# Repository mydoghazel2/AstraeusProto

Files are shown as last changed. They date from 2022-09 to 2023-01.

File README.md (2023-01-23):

# Astraeus

This is the github repo of the West Virginia University SRAD avionics project named Astraeus.

Astreaus is a student led project to develop cheap, open-source, and modular avionics. The goal is to create electronics for our competition rocket and for student use on personal rockets. 

Astraeus is the greek god of the wind and dusk to match not only the idea of our avionics being on a rocket but also our competition rocket being named "Dark and Dusty" after the song Country Roads 

# Final Design 
## Top Side
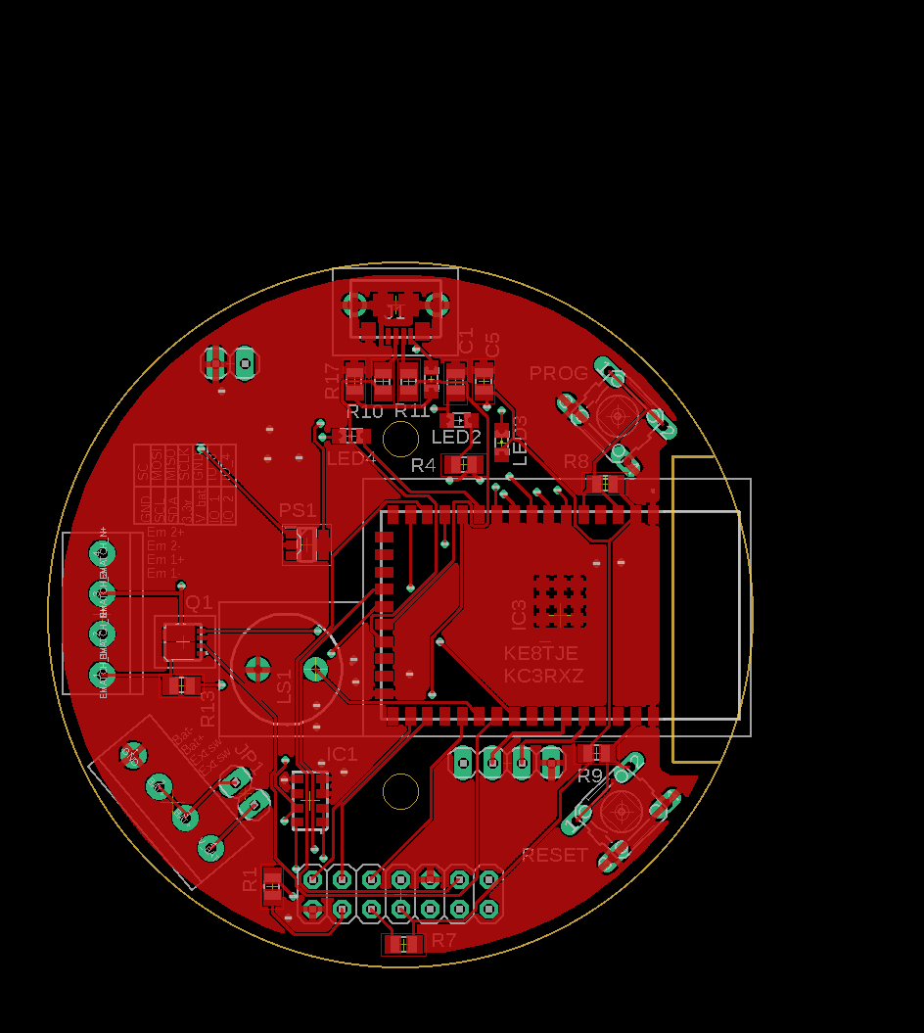
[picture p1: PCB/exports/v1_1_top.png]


## Bottom Side 
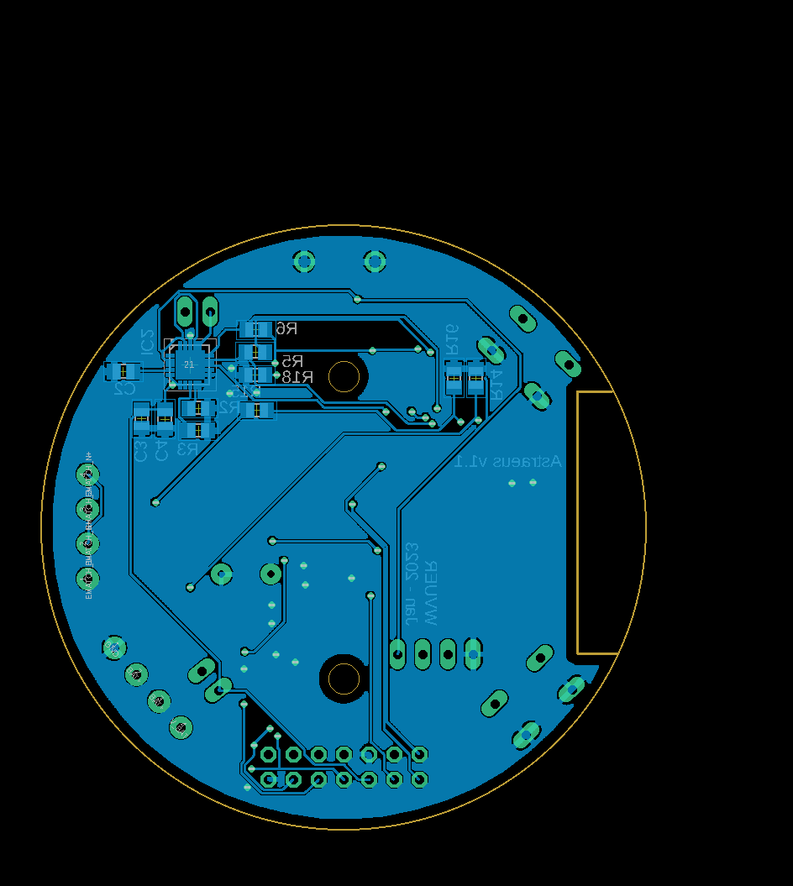
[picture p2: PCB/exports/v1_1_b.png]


# PCB

EAGLE is used as the PCB designing software. All the libraries needed is included in `./PCB/lib`

- if you are on linux. Use the following command to make a sim links to the default eagle save directory  

```
cd ~/EAGLE/projects
ln -s ~/Projects/Astraeus/PCB/ git-pcb
```

- if you are on windows 10: Add instructions on how to get EAGLE running

# TO-DO

- [x] Initial planning and requirement gathering.
- [x] Finalizing the hardware specification.
- [x] Schematic design
  - [x] BMS
  - [x] voltage regulation
  - [x] Sensors
  - [x] USB
  - [ ] upload/download
  - [ ] SD card

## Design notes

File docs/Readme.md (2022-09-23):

# WVUER Funded Project: Astraeus 

Author: [Gabriel Piatt](https://github.com/mydoghazel2)

WVUER is predominately an SRAD team using student created devices in competition and in personal rockets. However, historically we use “store-bought” electronic components aside from some electrical payloads our altimeters are always commercially available. Project Astraeus seeks to develop an altimeter family in house, fully developed, funded, and produced within West Virginia University with an emphasis on open-source development. The plan is divided into two stages, development, and testing. The development phase will be the Fall semester and will involve club members using an Intel or an ARM microcontroller and additional IC logic to design and create 6 circuit board variants ready to test.  The goal is to produce a pressure-based altimeter and related boards for under 25$ per board (end cost) and producing a full, thorough documentation on every step of the process. Including pictures, drawings, flight data, full cost breakdown, and videos. All to create a cheap and effective SRAD altimeter which can function within current altimeter standards and can compete with COTS altimeters. 

Major stages of development will include the decision and development of a breakout board which utilizes a microcontroller to act as the “brains” of the device. We will need to develop an inert flag which would pop and indicate a firing of a black powder charge. This will be used in phase two to test efficacy of the device at altitude. We will do preliminary pressure tests in a vacuum pot then send it as an inactive payload on student’s rockets in the spring semester. Hopefully, having at least 5 test flights of various heights. 

One of the development goals is to make the system somewhat modular, so various components can be added and removed as necessary to increase or decrease functionality as needed. I also aim to have similar total function as the Telemega with GPS, accelerometer, and of course deployment charges. Using a standardized microcontroller platform should make this easy as well as allowing our code and designs to be open source and available on GitHub or various platforms. 
The vision is a board with a microcontroller base, using GPS, accelerometers, and pressure sensors to collect data about flight and provide electronic deployments. The board will have a main section for the microcontroller and pressure sensor with the GPS and accelerometer devices being on separate boards (however probably printed on the same chip and removed post-manufacturing). These will plug into the main unit and several through holes and Molex connectors will allow for expansion or other sensors the be added. After retrieving the device data will be collected from a micro-SD card.

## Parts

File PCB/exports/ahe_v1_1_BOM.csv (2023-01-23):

Qty | Value | Device | Package | Parts | MOUSER_PRICE-STOCK | Description | ARROW_PART_NUMBER | ARROW_PRICE-STOCK | DESCRIPTION | HEIGHT | MANUFACTURER_NAME | MANUFACTURER_PART_NUMBER | MF | MOUSER_PART_NUMBER | MOUSER_TESTING_PART_NUMBER | MOUSER_TESTING_PRICE-STOCK | MPN | OC_FARNELL | OC_NEWARK | POPULARITY | SPICEPREFIX
2 |  | 10-XX | B3F-10XX | S1, S2 |  | OMRON SWITCH |  |  |  |  |  |  |  |  |  |  | B3F-1000 | 176432 | 36M3542 | 72
4 |  | LEDCHIPLED_0805 | CHIPLED_0805 | LED1, LED2, LED3, LED4 |  | LED
2 |  | PINHD-1X2 | 1X02 | JP1, JP4 |  | PIN HEADER |  |  |  |  |  |  |  |  |  |  |  |  |  | 98
1 |  | PINHD-1X4 | 1X04 | JP5 |  | PIN HEADER |  |  |  |  |  |  |  |  |  |  |  |  |  | 91
1 |  | PINHD-2X7 | 2X07 | JP2 |  | PIN HEADER |  |  |  |  |  |  |  |  |  |  |  |  |  | 8
2 | 100k | R-US_R0805 | R0805 | R13, R15 |  | RESISTOR, American symbol |  |  |  |  |  |  |  |  |  |  |  |  |  | 85 | R
1 | 100n | C-USC0805 | C0805 | C1 |  | CAPACITOR, American symbol |  |  |  |  |  |  |  |  |  |  |  |  |  | 63 | C
5 | 10k | R-US_R0805 | R0805 | R1, R6, R7, R8, R9 |  | RESISTOR, American symbol |  |  |  |  |  |  |  |  |  |  |  |  |  | 85 | R
1 | 10u | C-USC0805 | C0805 | C2 | https://www.mouser.com/ProductDetail/KEMET/C0805C106K8RACTU?qs=iP0bYSAMAFqUyr6Ql6ZwXw%3D%3D | CAPACITOR, American symbol |  |  |  |  |  |  |  |  |  |  |  |  |  | 63 | C
2 | 1X4-3.5MM | 1X4-3.5MM | 1X04-3.5MM | CN3, CN4 |  | 4-pin connector
2 | 1u | C-USC0805 | C0805 | C4, C5 | https://www.mouser.com/ProductDetail/KYOCERA-AVX/08055D105MAT2A?qs=OZ%252BC78tOsDZHSveO3HZ7XQ%3D%3D | CAPACITOR, American symbol |  |  |  |  |  |  |  |  |  |  |  |  |  | 63 | C
2 | 27k | R-US_R0805 | R0805 | R14, R16 |  | RESISTOR, American symbol |  |  |  |  |  |  |  |  |  |  |  |  |  | 85 | R
1 | 2k | R-US_R0805 | R0805 | R3 |  | RESISTOR, American symbol |  |  |  |  |  |  |  |  |  |  |  |  |  | 85 | R
2 | 33 | R-US_R0805 | R0805 | R10, R11 |  | RESISTOR, American symbol |  |  |  |  |  |  |  |  |  |  |  |  |  | 85 | R
4 | 330 | R-US_R0805 | R0805 | R4, R5, R17, R18 |  | RESISTOR, American symbol |  |  |  |  |  |  |  |  |  |  |  |  |  | 85 | R
1 | 4.7u | C-USC0805 | C0805 | C3 | https://www.mouser.com/ProductDetail/KYOCERA-AVX/08053D475MAT2A | CAPACITOR, American symbol |  |  |  |  |  |  |  |  |  |  |  |  |  | 63 | C
1 | 40k | R-US_R0805 | R0805 | R2 | https://www.mouser.com/ProductDetail/Vishay-Draloric/RCA080540K2FKEA?qs=ZSTLft15nNBGWXJNdNljew%3D%3D | RESISTOR, American symbol |  |  |  |  |  |  |  |  |  |  |  |  |  | 85 | R
1 | BU33SD5WG-TR | BU33SD5WG-TR | SOT95P280X125-5N | PS1 | https://www.mouser.co.uk/ProductDetail/ROHM-Semiconductor/BU33SD5WG-TR?qs=%2FKR40Cd6GUrQDzRkUEt69Q%3D%3D | LDO regulator,3.3V,0.5A,standby,SSOP5 ROHM BU33SD5WG-TR, LDO Voltage Regulator, 0.5A, 3.3 V +/-2%, 1.7 6 Vin, 5-Pin SSOP |  |  | LDO regulator,3.3V,0.5A,standby,SSOP5 ROHM BU33SD5WG-TR, LDO Voltage Regulator, 0.5A, 3.3 V +/-2%, 1.7 6 Vin, 5-Pin SSOP | 1.25mm | ROHM Semiconductor | BU33SD5WG-TR |  | 755-BU33SD5WG-TR
1 | CMI-9605-0580T | CMI-9605-0580T | CMI96050580T | LS1 | https://www.mouser.co.uk/ProductDetail/CUI-Devices/CMI-9605-0580T?qs=P1JMDcb91o49u9Yh70m6sw%3D%3D | Piezo Buzzers & Audio Indicators buzzer, 9.6 mm x 5 mm deep, M, 5 VDC, 80 dB, Through Hole, Audio Indicator |  |  | Piezo Buzzers & Audio Indicators buzzer, 9.6 mm x 5 mm deep, M, 5 VDC, 80 dB, Through Hole, Audio Indicator | 5mm | CUI Inc. | CMI-9605-0580T |  | 490-CMI-9605-0580T
1 | ESP32-S2-WROOM-I_M22S2H3200UH3 | ESP32-S2-WROOM-I_M22S2H3200UH3 | ESP32S2WROOMIM22S2H3200UH3Q0 | IC3 | https://www.mouser.co.uk/ProductDetail/Espressif-Systems/ESP32-S2-WROOM-IM22S2H3200UH3Q0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 | WiFi Modules (802.11) Module ESP32-S2 WROOM IPEX ANT |  |  | WiFi Modules (802.11) Module ESP32-S2 WROOM IPEX ANT | 3.45mm | Espressif Systems | ESP32-S2-WROOM-I(M22S2H3200UH3Q0) |  | 356-ESP32S2WRMI320UH
1 | MCP73871-1CCI_ML | MCP73871-1CCI_ML | QFN50P400X400X100-21N | IC2 | https://www.mouser.co.uk/ProductDetail/Microchip-Technology-Atmel/MCP73871-1CCI-ML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 | Battery Management USB/AC Battery Charger w/Pwr Mgmt |  |  | Battery Management USB/AC Battery Charger w/Pwr Mgmt | 1mm | Microchip | MCP73871-1CCI/ML |  | 579-MCP73871-1CCI/ML
1 | MS560702BA03-50 | MS560702BA03-50 | MS5607-02BA03 | IC1 | https://www.mouser.co.uk/ProductDetail/Measurement-Specialties/MS560702BA03-50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 | MS560702BA03-50, Barometric Pressure Sensor, 1200mbar 0 3.6 V Output, 8-Pin QFN |  |  | MS560702BA03-50, Barometric Pressure Sensor, 1200mbar 0 3.6 V Output, 8-Pin QFN | mm | TE Connectivity | MS560702BA03-50 |  | 824-MS560702BA03-50
1 | TSM200N03DPQ33_RGG | TSM200N03DPQ33_RGG | TSM200N03DPQ33RGG | Q1 | https://www.mouser.co.uk/ProductDetail/Taiwan-Semiconductor/TSM200N03DPQ33-RGG?qs=BZBei1rCqCAHGBwVoEKNiA%3D%3D | MOSFET MOSFET, Dual, N-Ch Trench, 30V, 20A |  |  | MOSFET MOSFET, Dual, N-Ch Trench, 30V, 20A | 0.8mm | Taiwan Semiconductor | TSM200N03DPQ33 RGG |  | 821-TSM200N03DPQ33RG
1 | USB3075-30-A | USB3075-30-A | USB307530A | J1 | https://www.mouser.co.uk/ProductDetail/GCT/USB3075-30-A?qs=KUoIvG%2F9IlbGMJplbp1ybA%3D%3D | GCT (GLOBAL CONNECTOR TECHNOLOGY) - USB3075-30-A - USB Connector, Micro USB Type B, USB 2.0, Receptacle, 5 Ways, Surface Mount, Right Angle |  |  | GCT (GLOBAL CONNECTOR TECHNOLOGY) - USB3075-30-A - USB Connector, Micro USB Type B, USB 2.0, Receptacle, 5 Ways, Surface Mount, Right Angle | 2.7mm | GCT (GLOBAL CONNECTOR TECHNOLOGY) | USB3075-30-A |  | 640-USB3075-30-A

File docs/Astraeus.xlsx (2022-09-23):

Component Desc. | Cost/Unit | Units | Total Cost
2 Gallon Vacuum Chamber with 5 CFM 1/3HP Single Stage Pump | 79.99 | 1 | 79.99 |  | Total BoM
ATTINY12V-1PU | 1.75 | 6 | 10.5 | <- or something | 550.0063077
4 Layer PCBs | 0.7692307692 | 10 | 7.692307692
pressure MS560702BA03-50 | 5.514 | 6 | 33.084
AT-1220-TT-R | 0.94 | 6 | 5.64
Micro-USB 10118192 | 0.43 | 6 | 2.58
1935187 terminal | 0.96 | 6 | 5.76
electronic "deadmatch" | 2 | 10 | 20
GPS NEO-6M | 12.79 | 2 | 25.58
Micro SD Card Micro SDHC Mini TF Card Adapter | 1.856 | 5 | 9.28
Various smaller components (resistors, transistors, etc.) | 100 | 1 | 100
ADXL343BCCZ-RL accel | 3.42 | 6 | 20.52
sea jump 3.7V 1200mAh Upgrade Li-Polymer Battery 5pcs+1PCS Battery Charger | 22.99 | 1 | 22.99
Adafruit 1.47" 320x172 Round Rectangle Color IPS TFT Display | 17.5 | 1 | 17.5
Cables | 10 | 1 | 10
Micro Sd Cards | 5 | 4 | 20
Solder | 15 | 1 | 15
Flah memory | 0.78 | 6 | 4.68
Shipping, Fees and breakage misc | 79.97 | 1 | 79.97
CC1200 | 2.54 | 6 | 15.24
Hardware and mounting | 35 | 1 | 35
Ps1240 Buzzer | 1.5 | 6 | 9

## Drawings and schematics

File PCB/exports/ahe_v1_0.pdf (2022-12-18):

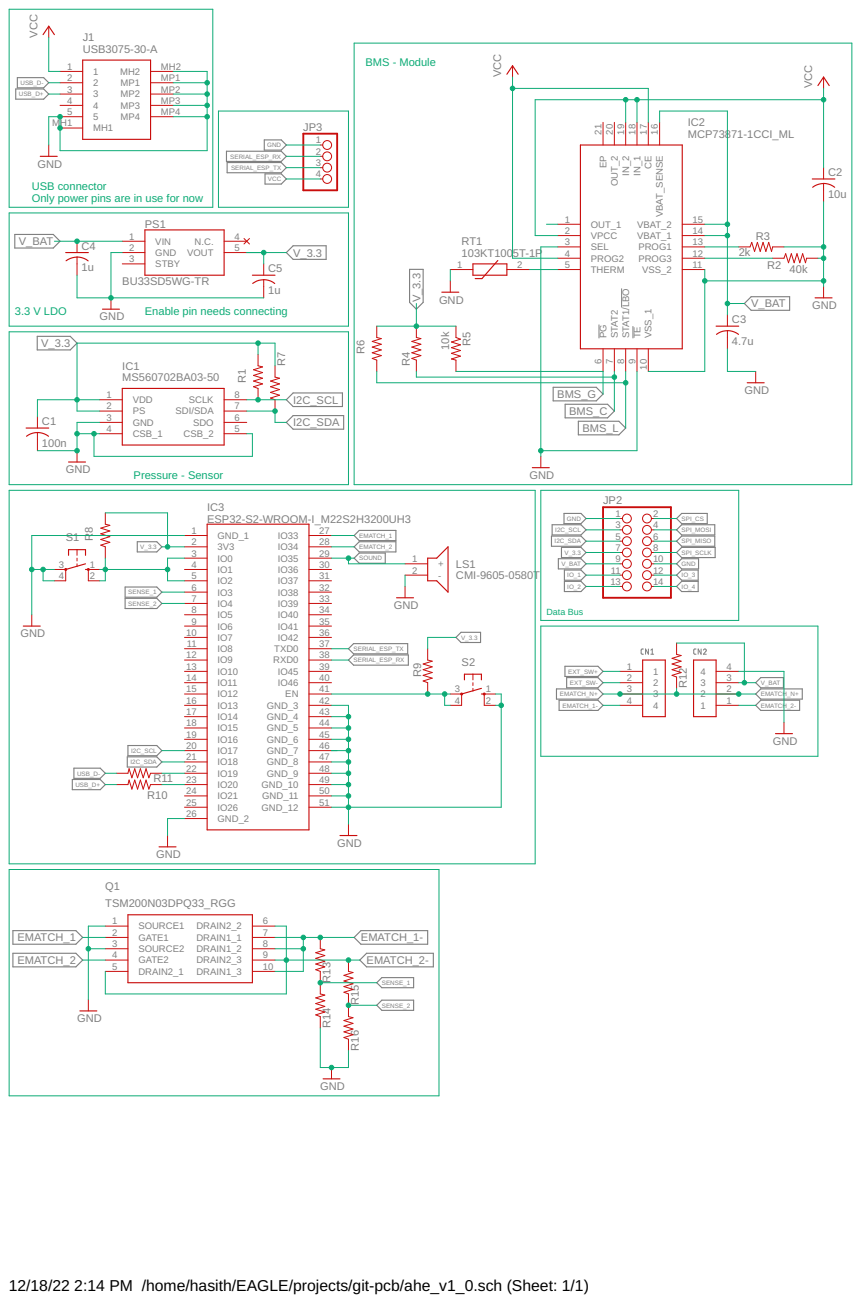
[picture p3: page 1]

BMS - Module

USB connector Only power pins are in use for now

3.3 V LDO

Enable pin needs connecting

12/18/22 2:14 PM /home/hasith/EAGLE/projects/git-pcb/ahe_v1_0.sch (Sheet: 1/1)

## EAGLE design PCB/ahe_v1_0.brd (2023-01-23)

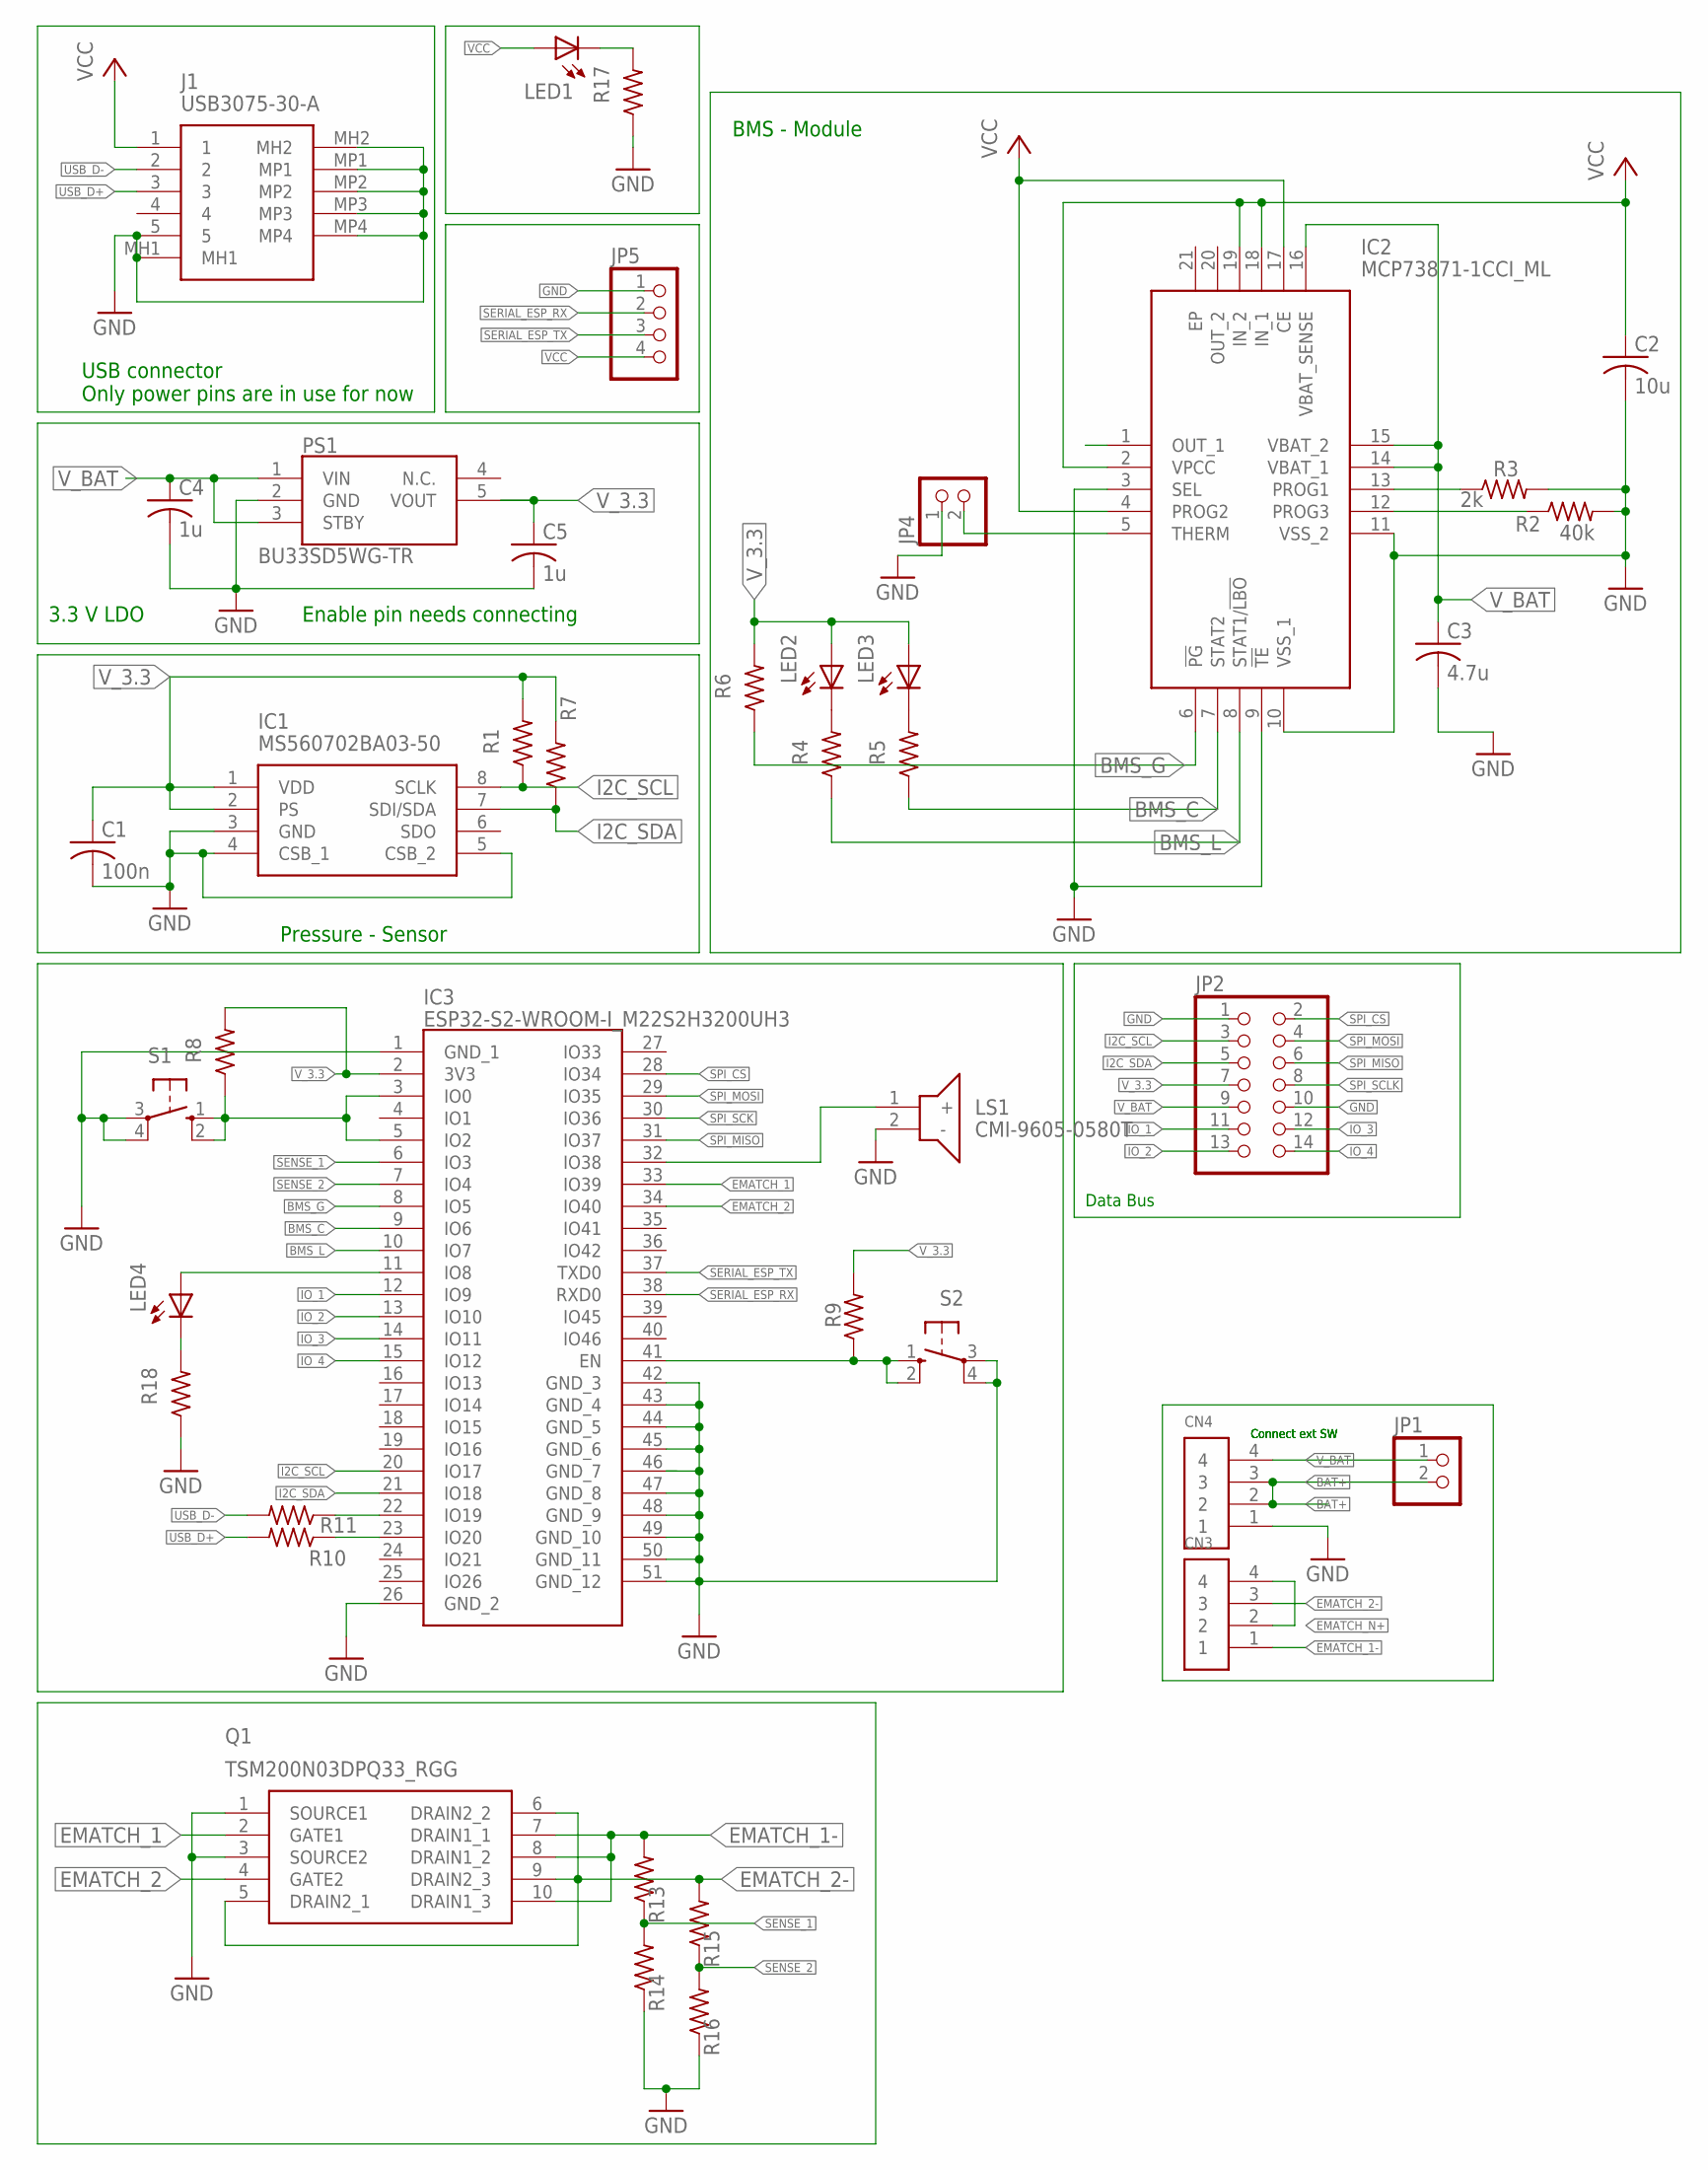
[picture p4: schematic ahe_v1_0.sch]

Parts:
C1: 100n; C0805
C2: 10u; C0805
C3: 4.7u; C0805
C4, C5: 1u; C0805
CN3, CN4: 1X4-3.5MM; 1X04-3.5MM
IC1: MS560702BA03-50; MS5607-02BA03
IC2: MCP73871-1CCI_ML; QFN50P400X400X100-21N
IC3: ESP32-S2-WROOM-I_M22S2H3200UH3; ESP32S2WROOMIM22S2H3200UH3Q0
J1: USB3075-30-A; USB307530A
JP1, JP4: PINHD-1X2; 1X02
JP2: PINHD-2X7; 2X07
JP5: PINHD-1X4; 1X04
LED1, LED2, LED3, LED4: LEDCHIPLED_0805; CHIPLED_0805
LS1: CMI-9605-0580T; CMI96050580T
PS1: BU33SD5WG-TR; SOT95P280X125-5N
Q1: TSM200N03DPQ33_RGG; TSM200N03DPQ33RGG
R1, R6, R7, R8, R9: 10k; R0805
R2: 40k; R0805
R3: 2k; R0805
R4, R5, R17, R18: 330; R0805
R10, R11: 33; R0805
R13, R15: 100k; R0805
R14, R16: 27k; R0805
S1, S2: 10-XX; B3F-10XX

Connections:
BAT+: CN4.2, CN4.3, JP1.2
BMS_C: IC2.7 (STAT2), IC3.9 (IO6), R5.1
BMS_G: IC2.6 (!PG), IC3.8 (IO5), R6.1
BMS_L: IC2.8 (STAT1/!LBO), IC3.10 (IO7), R4.1
EMATCH_1: IC3.33 (IO39), Q1.2 (GATE1)
EMATCH_1-: CN3.1, Q1.7 (DRAIN1_1), Q1.8 (DRAIN1_2), Q1.10 (DRAIN1_3), R13.2
EMATCH_2: IC3.34 (IO40), Q1.4 (GATE2)
EMATCH_2-: CN3.3, Q1.5 (DRAIN2_1), Q1.6 (DRAIN2_2), Q1.9 (DRAIN2_3), R15.2
EMATCH_N+: CN3.2, CN3.4
GND: C1.2, C2.2, C3.2, C4.2, C5.2, CN4.1, IC1.3 (GND), IC1.4 (CSB_1), IC1.5 (CSB_2), IC2.3 (SEL), IC2.9 (!TE), IC2.10 (VSS_1), IC2.11 (VSS_2), IC3.1 (GND_1), IC3.26 (GND_2), IC3.42 (GND_3), IC3.43 (GND_4), IC3.44 (GND_5), IC3.45 (GND_6), IC3.46 (GND_7), IC3.47 (GND_8), IC3.48 (GND_9), IC3.49 (GND_10), IC3.50 (GND_11), IC3.51 (GND_12), J1.5, J1.MH1, J1.MH2, J1.MP1, J1.MP2, J1.MP3, J1.MP4, JP2.1, JP2.10, JP4.1, JP5.1, LS1.2 (-), PS1.2 (GND), Q1.1 (SOURCE1), Q1.3 (SOURCE2), R2.2, R3.2, R14.1, R16.1, R17.1, R18.1, S1.3, S1.4 (P1), S2.3, S2.4 (P1)
I2C_SCL: IC1.8 (SCLK), IC3.20 (IO17), JP2.3, R1.1
I2C_SDA: IC1.7 (SDI/SDA), IC3.21 (IO18), JP2.5, R7.1
IO_1: IC3.12 (IO9), JP2.11
IO_2: IC3.13 (IO10), JP2.13
IO_3: IC3.14 (IO11), JP2.12
IO_4: IC3.15 (IO12), JP2.14
unnamed: IC2.13 (PROG1), R3.1
unnamed: IC2.12 (PROG3), R2.1
unnamed: IC2.5 (THERM), JP4.2
unnamed: IC3.3 (IO0), IC3.5 (IO2), R8.1, S1.1 (S), S1.2 (S1)
unnamed: IC3.22 (IO19), R11.1
unnamed: IC3.23 (IO20), R10.1
unnamed: LED1.C, R17.2
unnamed: LED2.C, R4.2
unnamed: LED3.C, R5.2
unnamed: LED4.C, R18.2
unnamed: IC3.11 (IO8), LED4.A
unnamed: IC3.41 (EN), R9.1, S2.1 (S), S2.2 (S1)
SENSE_1: IC3.6 (IO3), R13.1, R14.2
SENSE_2: IC3.7 (IO4), R15.1, R16.2
SERIAL_ESP_RX: IC3.38 (RXD0), JP5.2
SERIAL_ESP_TX: IC3.37 (TXD0), JP5.3
SOUND: IC3.32 (IO38), LS1.1 (+)
SPI_CS: IC3.28 (IO34), JP2.2
SPI_MISO: IC3.31 (IO37), JP2.6
SPI_MOSI: IC3.29 (IO35), JP2.4
SPI_SCK: IC3.30 (IO36)
SPI_SCLK: JP2.8
USB_D+: J1.3, R10.2
USB_D-: J1.2, R11.2
VCC: C2.1, IC2.2 (VPCC), IC2.4 (PROG2), IC2.17 (CE), IC2.18 (IN_1), IC2.19 (IN_2), J1.1, JP5.4, LED1.A
V_3.3: C1.1, C5.1, IC1.1 (VDD), IC1.2 (PS), IC3.2 (3V3), JP2.7, LED2.A, LED3.A, PS1.5 (VOUT), R1.2, R6.2, R7.2, R8.2, R9.2
V_BAT: C3.1, C4.1, CN4.4, IC2.14 (VBAT_1), IC2.15 (VBAT_2), IC2.16 (VBAT_SENSE), JP1.1, JP2.9, PS1.1 (VIN), PS1.3 (STBY)

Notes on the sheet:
Pressure - Sensor
Enable pin needs connecting
USB connector Only power pins are in use for now
3.3 V LDO
BMS - Module
Data Bus
Connect ext SW

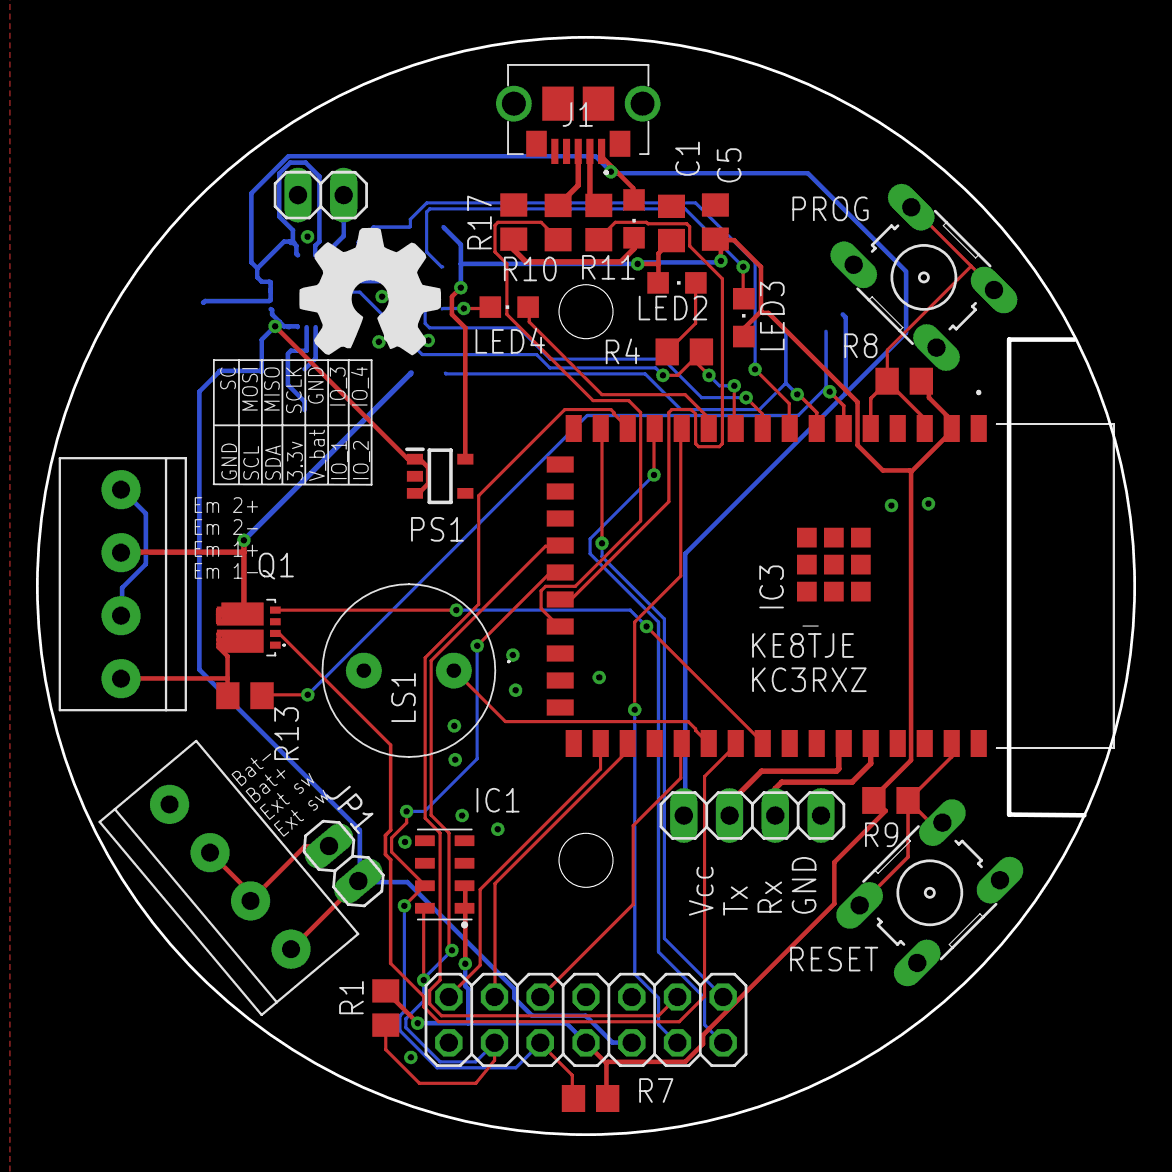
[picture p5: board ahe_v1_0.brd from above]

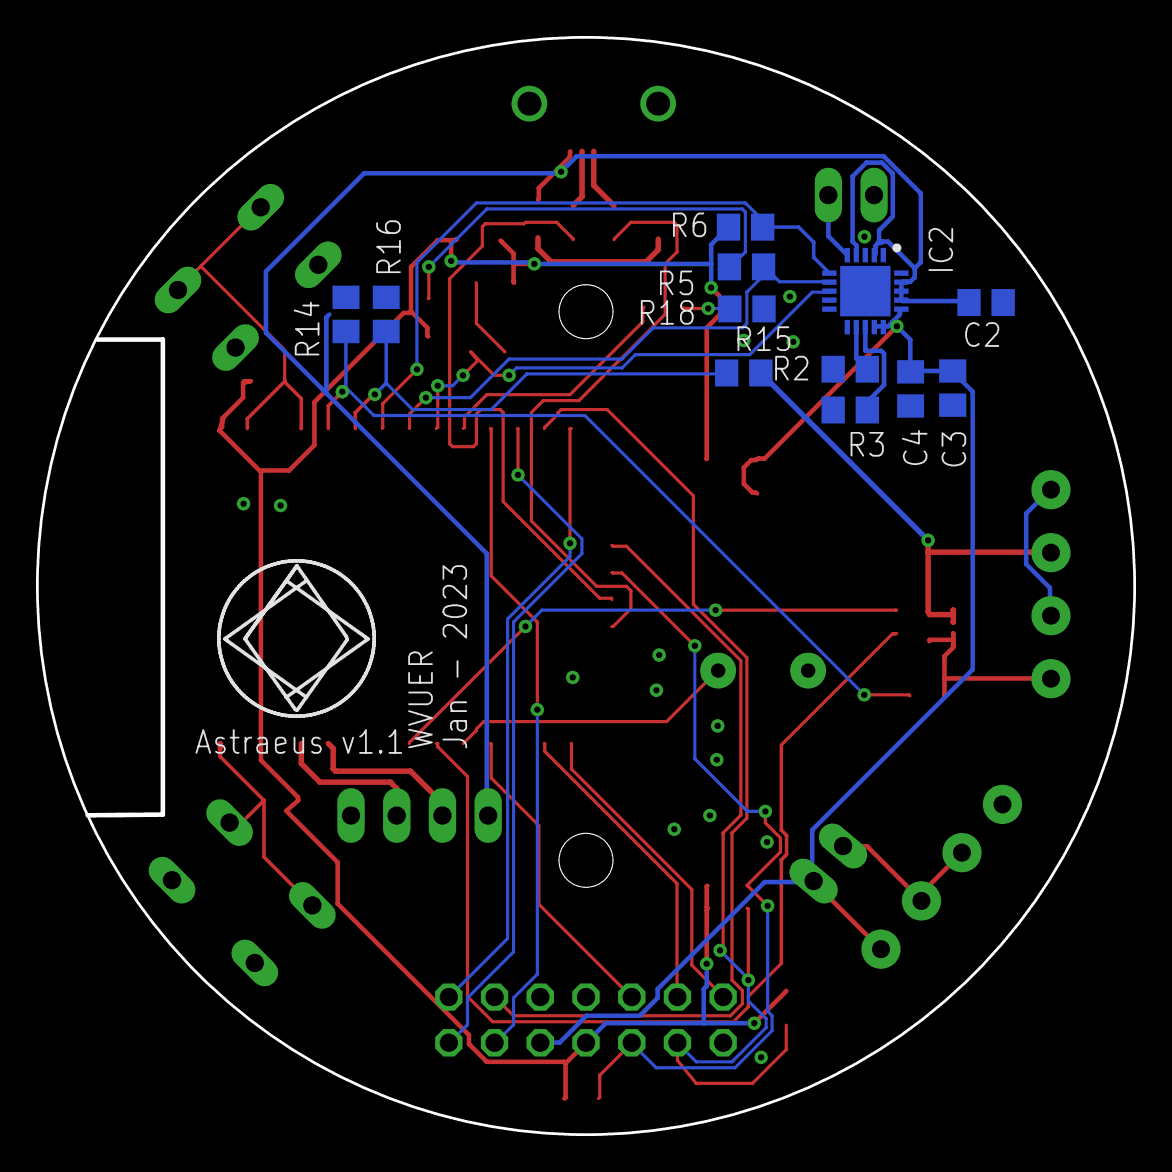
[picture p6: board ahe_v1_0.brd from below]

Board: 2 copper layers, 61.0 x 61.0 mm, 41 parts (12 on the bottom side), 41 nets.

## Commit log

2022-09-23 Initial Commit with Proposal and Budget
    [Astraeus.xlsx]
2022-09-23 moved documentation to docs
    [Astraeus.xlsx]
2022-11-15 Added the eagel PCB project files to ./PCB
    [ahe_v1_0.sch]
2022-11-15 updated the readme with eagle usage instructions
    [ahe_v1_0.sch]
2022-11-30 added an LDO
    [ahe_v1_0.sch]
2022-12-01 added some cosmatics to completed parts
    [ahe_v1_0.sch]
2022-12-09 Updated the BMS i/o
    [ahe_v1_0.sch]
2022-12-09 modified BMS
    [ahe_v1_0.sch]
2022-12-15 Completed BMS/LDO
    [ahe_v1_0.sch]
2022-12-16 #6 pressure sensor completed
    [ahe_v1_0.sch]
2022-12-17 updated the ESP32 library to match actual product
    [ahe_v1_0.sch]
2022-12-18 #5 #2 added databus and basic IO
    [ahe_v1_0.sch]
2022-12-18 full schematic
    [ahe_v1_0.sch, ahe_v1_0_BOM.csv]
2022-12-18 added costing to the BOM
    [ahe_v1_0_BOM.csv]
2022-12-20 added SPI from the ESP
    [ahe_v1_0.sch]
2022-12-21 #2 board 1 with lipo mounted on the back
    [ahe_v1_0.sch, ahe_v1_1.brd]
2022-12-21 added board file
    [ahe_v1_0.brd]
2022-12-21 removed v1_1 junk version
    [ahe_v1_1.brd]
2022-12-21 added information on the board design
2022-12-21 fixed schematic bugs in v1_0
    [ahe_v1_0.brd, ahe_v1_0.sch]
2022-12-22 Final schematic and board for ESP32-S2
    [ahe_v1_0.brd, ahe_v1_0.sch]
2022-12-22 Added PCB images
2022-12-22 Added serial labels.
    [ahe_v1_0.brd]
2022-12-23 updated BOM with links
    [ahe_v1_1_BOM.csv]
2022-12-23 Added logo to silk screens
    [ahe_v1_0.brd]
